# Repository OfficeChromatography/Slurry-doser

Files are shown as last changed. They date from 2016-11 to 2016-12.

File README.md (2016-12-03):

Slurry doser
===========

Open-source-based 3D printing of thin silica gel layers in planar chromatography

<br />This work is licensed under a <a rel="license" href="http://creativecommons.org/licenses/by-sa/4.0/">Creative Commons Attribution-ShareAlike 4.0 International License</a>.

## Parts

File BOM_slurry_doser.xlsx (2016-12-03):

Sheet: BOM hbot v0.1 Reprap
Name | Reference | Link manufacturer | Price per unit (Euro VAT) | Amount | Price total (Euro VAT)
Prusa i3 rework | 1234568399 | www.reprap-3d-printer.com | 550 | 1 | 550
Syringe moving | Printed | NA | 0 | 1 | 0
Syringe holder | Printed | NA | 0 | 1 | 0
Syringe caps | Printed | NA | 0 | 1 | 0
Motor holder | Printed | NA | 0 | 1 | 0
Coupler | Printed | NA | 0 | 1 | 0
Smooth shafts 6 mm | 1234568567 | www.reprap-3d-printer.com | 18 | 1 | 18
Linear bearing lm6uu | 1234568275 | www.reprap-3d-printer.com | 1.9 | 2 | 3.8
Trapezoidal lead screw 8 mm and nut | B01E5GS33U | www.amazon.de | 3.3 | 1 | 3.3
Nema 17 | 312 | www.reprap-3d-printer.com | 16 | 1 | 16
Inductive sensor | 1234568401 | www.reprap-3d-printer.com | 15 | 1 | 15
ABS, 1kg | 1234568224 | www.reprap-3d-printer.com | 21 | 1 | 21
Syringe, 10 mL | 4616103V | us.bbraunoem.com | 1 | 1 | 1
Syringe needle, 1.20 x 50 mm | 4667123 | us.bbraunoem.com | 1 | 1 | 1
Screw M3 x 30 | NA | local hardware store | 0 | 5 | 0
Screw M4 x 20 | NA | local hardware store | 0 | 4 | 0
Nut M4 | NA | local hardware store | 0 | 4 | 0
 | Total slurry doser (Euro) |  |  |  | 79.1
 | Total modified 3D printer (Euro) |  |  |  | 629.1

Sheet: Caulculation layer price
Materials | Cost per gram (Euro) | Weight (g) for flat layer, 100% of 4 mL | Weight (g) for channeled layer, 30% of 2 mL
Silica gel | 0.252 | 0.88 | 0.132
Calcium sulfate | 0.226 | 0.12 | 0.018
 | Total price | 0.25 Euro | 0.04 Euro

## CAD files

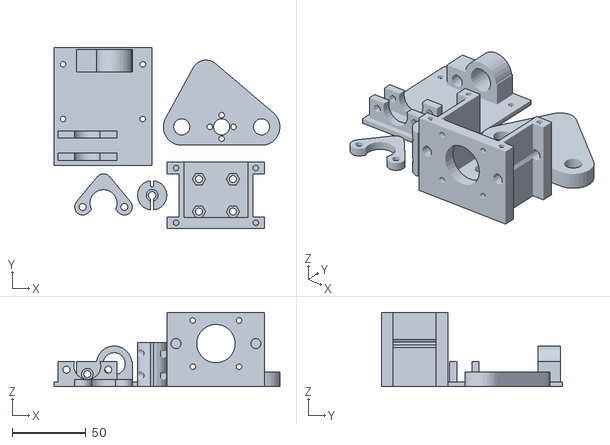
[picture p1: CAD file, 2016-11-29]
Slurry doser/TLC_printing_full_device.stl
153.0 x 122.7 x 50.3

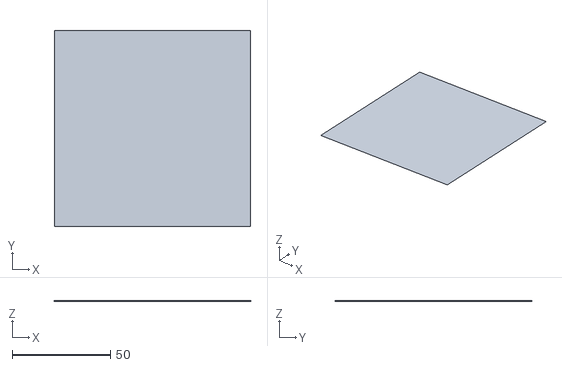
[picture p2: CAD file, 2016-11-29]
Layers/100*100*02.stl
100.0 x 100.0 x 0.2

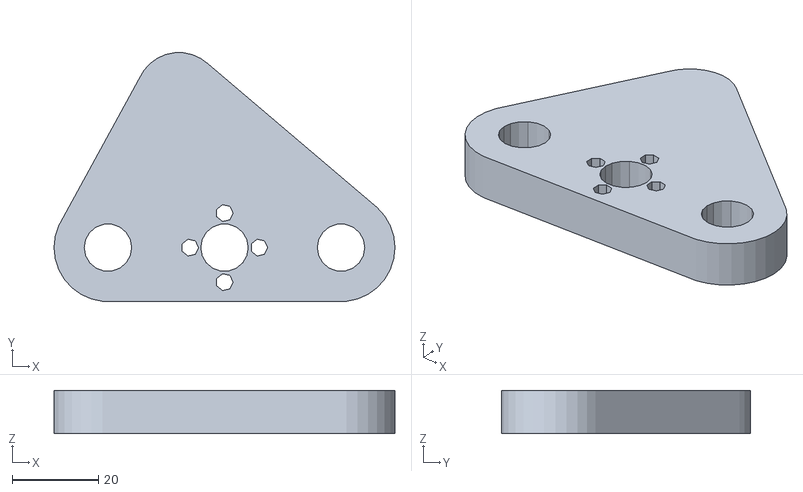
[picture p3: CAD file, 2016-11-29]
Slurry doser/Syringe_moving_bushing.stl
79.0 x 57.6 x 10.0

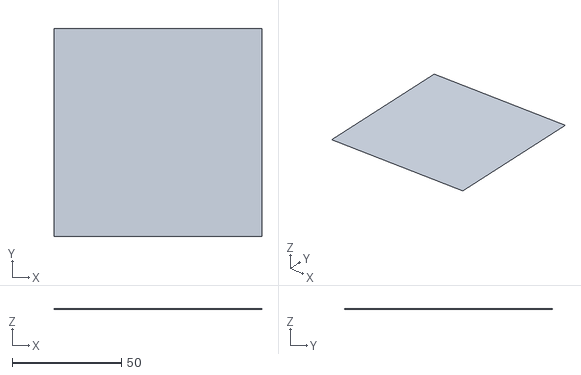
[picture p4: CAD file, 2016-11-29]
Layers/95*95*02.stl
95.0 x 95.0 x 0.2

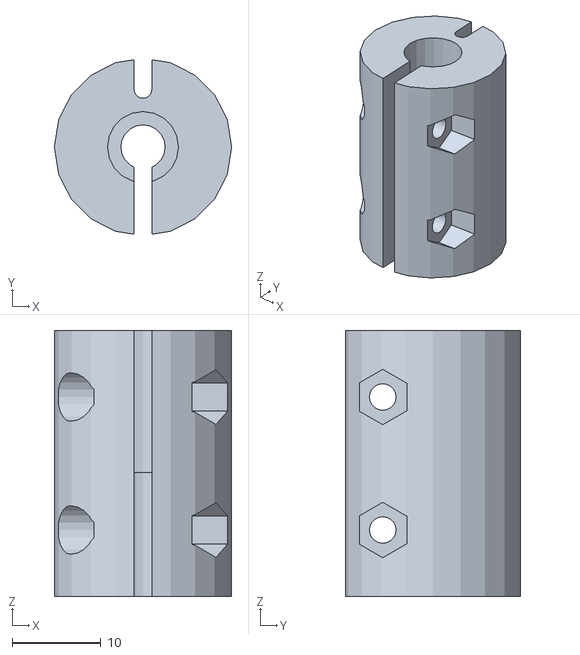
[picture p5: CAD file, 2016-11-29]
Slurry doser/coupler.stl
20.0 x 19.7 x 30.0

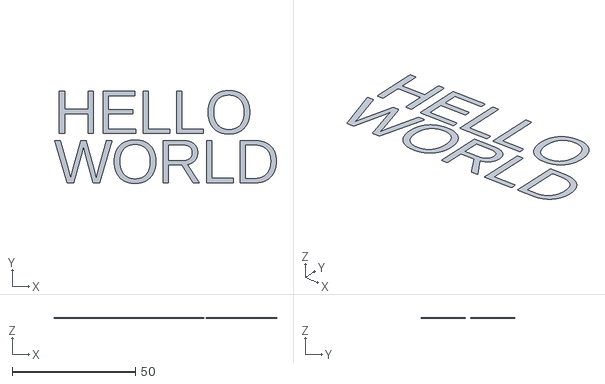
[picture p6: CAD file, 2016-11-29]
Layers/Hello world.stl
89.9 x 37.7 x 0.2

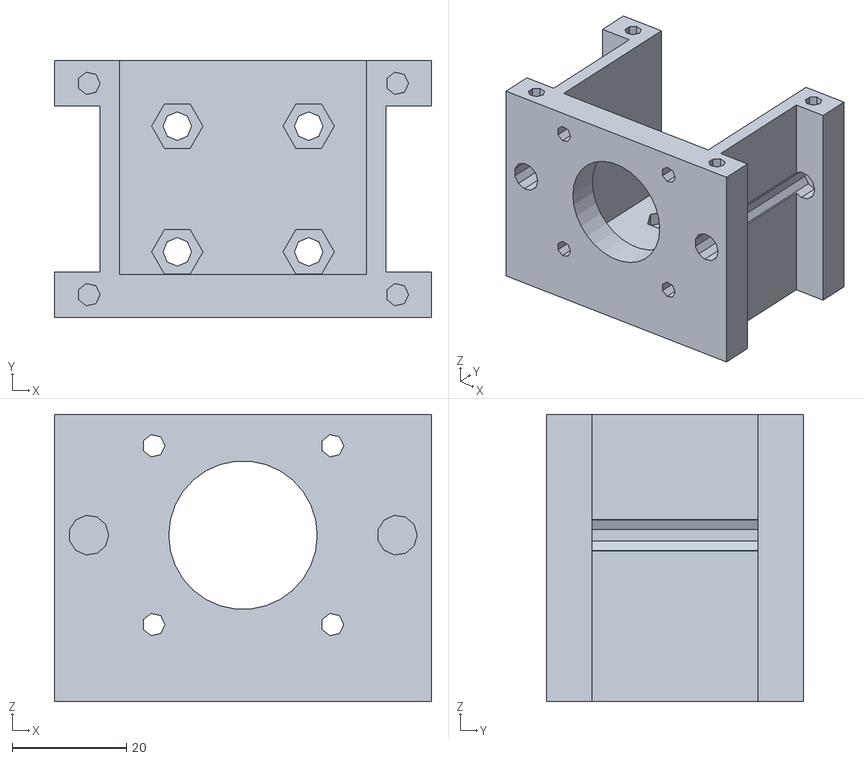
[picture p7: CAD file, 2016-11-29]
Slurry doser/Motor_holder.stl
66.0 x 45.0 x 50.3

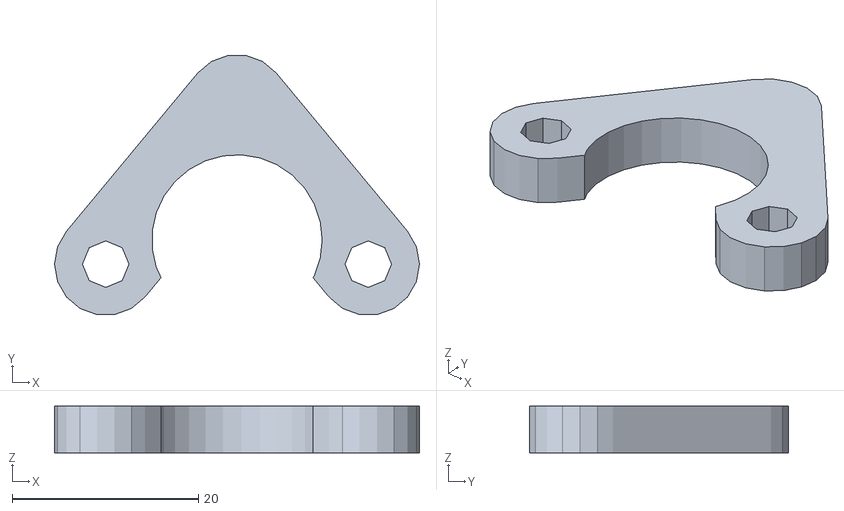
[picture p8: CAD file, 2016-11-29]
Slurry doser/Syringe_caps.stl
39.2 x 27.8 x 5.00

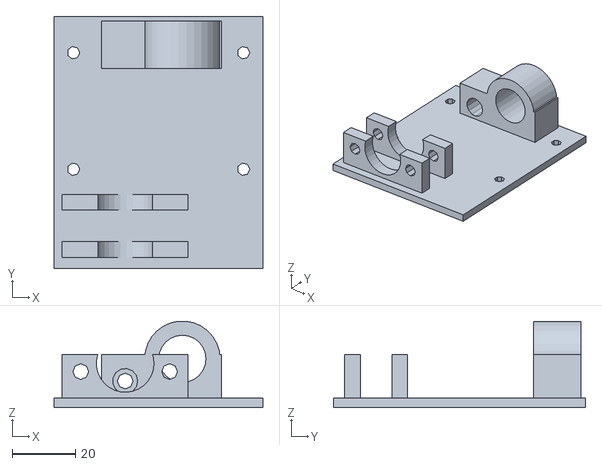
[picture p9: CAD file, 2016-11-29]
Slurry doser/Syringe_holder.stl
66.3 x 80.0 x 27.5

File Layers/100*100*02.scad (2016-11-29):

// Simple cube object with a given dimension   

cube([100,100,0.2],center=true);

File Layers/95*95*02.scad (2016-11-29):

// Simple cube object with a given dimension   

cube([95,95,0.2],center=true);

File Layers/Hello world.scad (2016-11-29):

 linear_extrude(0.2) text("HELLO", font = "Liberation Sans", size = 19, direction = "ltr", spacing = 1 );
 linear_extrude(0.2) translate([0,-20,0]) text("WORLD", font = "Liberation Sans", size = 19, direction = "ltr", spacing = 1 );

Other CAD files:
Slurry doser/Syringe_moving_lm6uu.stl
Slurry doser/adaptation_prusa_v05.scad
Slurry doser/Slurry_doser.scad
Slurry doser/coupler.scad
Slurry doser/vitamine.scad

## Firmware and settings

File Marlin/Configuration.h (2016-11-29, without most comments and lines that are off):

#define CONFIGURATION_H
#define STRING_VERSION_CONFIG_H __DATE__ " " __TIME__ // build date and time
#define STRING_CONFIG_H_AUTHOR "(none, default config)" // Who made the changes.
#define SERIAL_PORT 0
#define BAUDRATE 115200
#define MOTHERBOARD 33
#define EXTRUDERS 1
#define POWER_SUPPLY 1
#define TEMP_SENSOR_0 0
#define TEMP_SENSOR_1 0
#define TEMP_SENSOR_2 0
#define TEMP_SENSOR_BED 1
#define MAX_REDUNDANT_TEMP_SENSOR_DIFF 10
#define TEMP_RESIDENCY_TIME 10  // (seconds)
#define TEMP_HYSTERESIS 3       // (degC) range of +/- temperatures considered "close" to the target one
#define TEMP_WINDOW     1       // (degC) Window around target to start the residency timer x degC early.
#define HEATER_0_MINTEMP 5
#define HEATER_1_MINTEMP 5
#define HEATER_2_MINTEMP 5
#define BED_MINTEMP 5
#define HEATER_0_MAXTEMP 275
#define HEATER_1_MAXTEMP 275
#define HEATER_2_MAXTEMP 275
#define BED_MAXTEMP 150
#define PIDTEMP
#define BANG_MAX 225 // limits current to nozzle while in bang-bang mode; 255=full current
#define PID_MAX 225 // limits current to nozzle while PID is active (see PID_FUNCTIONAL_RANGE below); 255=full current
  #define PID_FUNCTIONAL_RANGE 10 // If the temperature difference between the target temperature and the actual temperature
  #define PID_INTEGRAL_DRIVE_MAX 255  //limit for the integral term
  #define K1 0.95 //smoothing factor within the PID
  #define PID_dT ((OVERSAMPLENR * 10.0)/(F_CPU / 64.0 / 256.0)) //sampling period of the temperature routine
    #define  DEFAULT_Kp 22.2
    #define  DEFAULT_Ki 1.08
    #define  DEFAULT_Kd 114
#define MAX_BED_POWER 225 // limits duty cycle to bed; 255=full current
#define ENDSTOPPULLUPS // Comment this out (using // at the start of the line) to disable the endstop pullup resistors
  #define ENDSTOPPULLUP_XMAX
  #define ENDSTOPPULLUP_YMAX
  #define ENDSTOPPULLUP_ZMAX
  #define ENDSTOPPULLUP_XMIN
  #define ENDSTOPPULLUP_YMIN
  #define ENDSTOPPULLUP_ZMIN
const bool X_MIN_ENDSTOP_INVERTING = true; // set to true to invert the logic of the endstop.
const bool Y_MIN_ENDSTOP_INVERTING = true; // set to true to invert the logic of the endstop.
const bool Z_MIN_ENDSTOP_INVERTING = true; // set to true to invert the logic of the endstop.
const bool X_MAX_ENDSTOP_INVERTING = true; // set to true to invert the logic of the endstop.
const bool Y_MAX_ENDSTOP_INVERTING = true; // set to true to invert the logic of the endstop.
const bool Z_MAX_ENDSTOP_INVERTING = true; // set to true to invert the logic of the endstop.
#if defined(COREXY) && !defined(DISABLE_MAX_ENDSTOPS)
  #define DISABLE_MAX_ENDSTOPS
#endif
#define X_ENABLE_ON 0
#define Y_ENABLE_ON 0
#define Z_ENABLE_ON 0
#define E_ENABLE_ON 0 // For all extruders
#define DISABLE_X false
#define DISABLE_Y false
#define DISABLE_Z false
#define DISABLE_E false // For all extruders
#define DISABLE_INACTIVE_EXTRUDER true //disable only inactive extruders and keep active extruder enabled
#define INVERT_X_DIR true    // for Mendel set to false, for Orca set to true
#define INVERT_Y_DIR true    // for Mendel set to true, for Orca set to false
#define INVERT_Z_DIR true     // for Mendel set to false, for Orca set to true
#define INVERT_E0_DIR false   // for direct drive extruder v9 set to true, for geared extruder set to false
#define INVERT_E1_DIR false    // for direct drive extruder v9 set to true, for geared extruder set to false
#define INVERT_E2_DIR false   // for direct drive extruder v9 set to true, for geared extruder set to false
#define X_HOME_DIR -1
#define Y_HOME_DIR -1
#define Z_HOME_DIR -1
#define min_software_endstops true // If true, axis won't move to coordinates less than HOME_POS.
#define max_software_endstops true  // If true, axis won't move to coordinates greater than the defined lengths below.
#define X_MAX_POS 200
#define X_MIN_POS 0
#define Y_MAX_POS 100
#define Y_MIN_POS 0
#define Z_MAX_POS 50
#define Z_MIN_POS 0
#define X_MAX_LENGTH (X_MAX_POS - X_MIN_POS)
#define Y_MAX_LENGTH (Y_MAX_POS - Y_MIN_POS)
#define Z_MAX_LENGTH (Z_MAX_POS - Z_MIN_POS)
#define ENABLE_AUTO_BED_LEVELING // Delete the comment to enable (remove // at the start of the line)
#define Z_PROBE_REPEATABILITY_TEST  // If not commented out, Z-Probe Repeatability test will be included if Auto Bed Leveling is Enabled.
      #define ABL_PROBE_PT_1_X 22
      #define ABL_PROBE_PT_1_Y 5
      #define ABL_PROBE_PT_2_X 100
      #define ABL_PROBE_PT_2_Y 80
      #define ABL_PROBE_PT_3_X 100
      #define ABL_PROBE_PT_3_Y 5
  #define X_PROBE_OFFSET_FROM_EXTRUDER 21
  #define Y_PROBE_OFFSET_FROM_EXTRUDER 0
  #define Z_PROBE_OFFSET_FROM_EXTRUDER 0 //M851 Z-"..." to change and save with M500.
  #define Z_RAISE_BEFORE_HOMING 1       // (in mm) Raise Z before homing (G28) for Probe Clearance.
  #define XY_TRAVEL_SPEED 9000         // X and Y axis travel speed between probes, in mm/min
  #define Z_RAISE_BEFORE_PROBING 1    //How much the extruder will be raised before traveling to the first probing point.
  #define Z_RAISE_BETWEEN_PROBINGS 1  //How much the extruder will be raised when traveling from between next probing points
  #define Z_SAFE_HOMING   // This feature is meant to avoid Z homing with probe outside the bed area.
    #define Z_SAFE_HOMING_X_POINT (50)    // X point for Z homing when homing all axis (G28)
    #define Z_SAFE_HOMING_Y_POINT (50)    // Y point for Z homing when homing all axis (G28)
#define MANUAL_X_HOME_POS 0
#define MANUAL_Y_HOME_POS 0
#define MANUAL_Z_HOME_POS 0
#define NUM_AXIS 4 // The axis order in all axis related arrays is X, Y, Z, E
#define HOMING_FEEDRATE {50*60, 50*60, 2*60, 0}  // set the homing speeds (mm/min)
#define DEFAULT_AXIS_STEPS_PER_UNIT   {80,80,4000,400}  // default steps per unit for Ultimaker
#define DEFAULT_MAX_FEEDRATE          {200, 200, 2, 35}    // (mm/sec)
#define DEFAULT_MAX_ACCELERATION      {2000,2000,20,2000}    // X, Y, Z, E maximum start speed for accelerated moves. E default values are good for Skeinforge 40+, for older versions raise them a lot.
#define DEFAULT_ACCELERATION          2000    // X, Y, Z and E max acceleration in mm/s^2 for printing moves
#define DEFAULT_RETRACT_ACCELERATION  2000   // X, Y, Z and E max acceleration in mm/s^2 for retracts
#define DEFAULT_XYJERK                20.0    // (mm/sec)
#define DEFAULT_ZJERK                 0.4     // (mm/sec)
#define DEFAULT_EJERK                 5.0    // (mm/sec)
#define CUSTOM_M_CODES
  #define CUSTOM_M_CODE_SET_Z_PROBE_OFFSET 851
  #define Z_PROBE_OFFSET_RANGE_MIN -15
  #define Z_PROBE_OFFSET_RANGE_MAX 0
#define EEPROM_SETTINGS
#define EEPROM_CHITCHAT
#define PLA_PREHEAT_HOTEND_TEMP 200
#define PLA_PREHEAT_HPB_TEMP 55
#define PLA_PREHEAT_FAN_SPEED 255   // Insert Value between 0 and 255
#define ABS_PREHEAT_HOTEND_TEMP 240
#define ABS_PREHEAT_HPB_TEMP 90
#define ABS_PREHEAT_FAN_SPEED 255   // Insert Value between 0 and 255
#define REPRAP_DISCOUNT_SMART_CONTROLLER
 #define ULTIPANEL
 #define NEWPANEL
  #define SDSUPPORT
  #define ULTRA_LCD
    #define LCD_WIDTH 20
    #define LCD_HEIGHT 4
#define SOFT_PWM_SCALE 0
#define NUM_SERVOS 1 // Servo index starts with 0 for M280 command
#define SERVO_ENDSTOPS {-1, -1, 0} // Servo index for X, Y, Z. Disable with -1
#define SERVO_ENDSTOP_ANGLES {0,0, 0,0, 20,90} // X,Y,Z Axis Extend and Retract angles
#define FILAMENT_SENSOR
#define FILAMENT_SENSOR_EXTRUDER_NUM	0  //The number of the extruder that has the filament sensor (0,1,2)
#define MEASUREMENT_DELAY_CM			14  //measurement delay in cm.  This is the distance from filament sensor to middle of barrel
#define DEFAULT_NOMINAL_FILAMENT_DIA  3.0  //Enter the diameter (in mm) of the filament generally used (3.0 mm or 1.75 mm) - this is then used in the slicer software.  Used for sensor reading validation
#define MEASURED_UPPER_LIMIT          3.30  //upper limit factor used for sensor reading validation in mm
#define MEASURED_LOWER_LIMIT          1.90  //lower limit factor for sensor reading validation in mm
#define MAX_MEASUREMENT_DELAY			20  //delay buffer size in bytes (1 byte = 1cm)- limits maximum measurement delay allowable (must be larger than MEASUREMENT_DELAY_CM  and lower number saves RAM)
#define DEFAULT_MEASURED_FILAMENT_DIA  DEFAULT_NOMINAL_FILAMENT_DIA  //set measured to nominal initially
#include "Configuration_adv.h"
#include "thermistortables.h"
